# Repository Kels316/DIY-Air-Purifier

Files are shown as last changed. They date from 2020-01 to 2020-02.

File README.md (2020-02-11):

# DIY-Air-Purifier
A small DIY air purifier using off-the-shelf components for &lt;$100.

Time to assemble this project - 1hr (not including 3D print time).

Uses a 3D printed housing so you'll need a printer or access to one. You could use a printing service such as 3D Hubs.

All prices listed are in AUD.

PLEASE READ THE SECTION ON TESTING BEFORE BUILDING THIS UNIT.

## Background
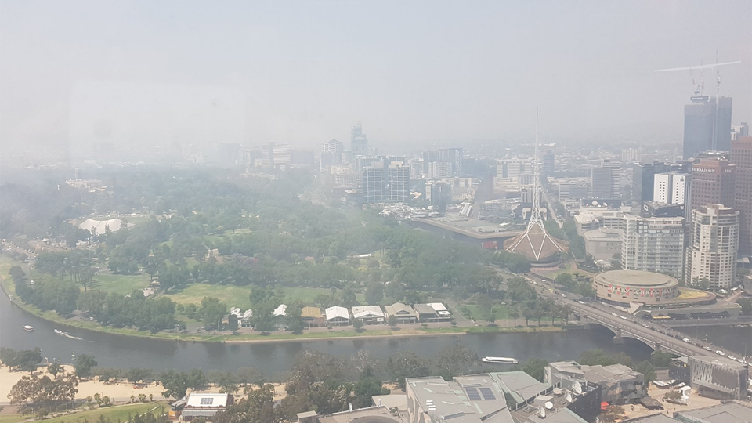
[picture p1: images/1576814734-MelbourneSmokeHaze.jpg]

In the summer of 2019/2020 Australia is experiencing unprecedented dangerous fire conditions driven by climate change. Much of the east coast of the country south of Brisbane is engulfed in deadly bushfires and air pollution ratings in cities such as Sydney, Canberra, Melbourne and many other regional cities and towns is many times the recommended safe levels of PM2.5 particles. The long term affects of the inhalation of bushfire smoke is mostly unknown at this time, but already people have died from respiratory distress bought about by the smoke-filled air.

There has been a great deal of discussion online and in the media about the use of P2 respirators and home air purifiers to reduce the effects of the bushfire smoke. However, information about the efficiacy of P2 respirators for bushfire smoke is not readily available and what information can be found suggests they may be of limited use. Health officials are continuing to recommend eliminating exposure to PM2.5 particles and bushfire smoke-related chemicals by remaining indoors if possible. Unfortunately for many people the summer heat makes indoors extremely uncomfortable and the evaporative air conditioners installed in many homes in my state of Victoria do not filter the damaging PM2.5 particles from the air. Health officials recommend using HEPA H13 air purifiers, however these are extremely expensive with even a basic unit suitable for a single room costing around $500.

With all this in mind I set about finding a way to build a low-cost, effective air purifier that would meet the minimum requirement to filter PM2.5 particles in a bedroom, so that children and at-risk people could at least sleep without inhaling these dangerous airborne contaminants.

This github sets out the process I followed to construct and test the device, as well as the BOM and 3D print STL files for recreating the device.

## Purpose
The purpose of this project is to create a small air purifier suitable for a bedroom or caravan (or similar sized space) that meets the following critiera:
  - Costs under $100 to build (in parts);
  - Can be constructed with relatively low levels of technical skill (there is soldering of two wires required);
  - Uses off-the-shelf components available in most Australian cities, or by order over the internet from Australian suppliers; and
  - Uses a HEPA H13 rated filter; and
  - Is powered from a commonly available USB powerbank.

## Method
I selected a readily available HEPA H13 rated filter normally used in cheap vacuum cleaners and available from Bunnings Warehouse. The rest of the air purifier is based around that filter. I then selected a range of 120mm computer fans with relatively high static pressure ratings (>2.0 mmAq) that could operate on 12vDC. As the fans are 12vDC I used a USB 'booster cable' which steps-up the voltage of any USB-A port from 5v to 12v; these cables are available online or from a range of electronics shops such as Jaycar.
After selecting the components I then designed a fan housing using Fusion 360 that provides the interface between the 120mm and the HEPA filter. The filter comes with a removable seal/cover at one end, so I use that end as the base of the unit and fit the fan to the top.
After basic testing with a small smoke generator to ensure the selected fans could draw air through the filter to a reasonable standard I have determined the project suitable for release so others can create their own version of this device both for use in their homes and for further testing.

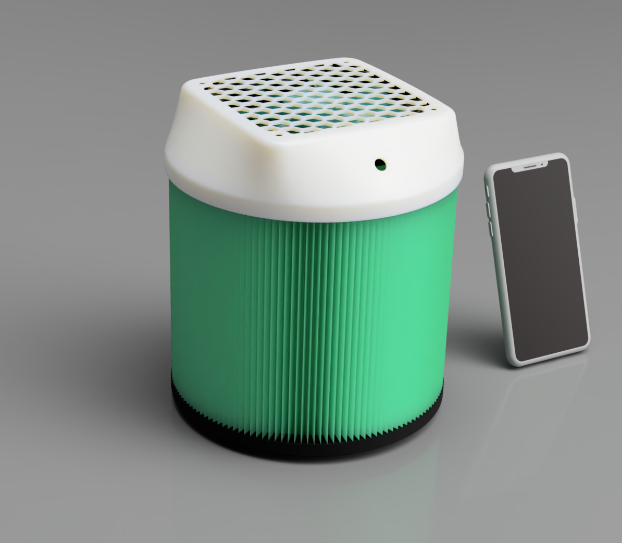
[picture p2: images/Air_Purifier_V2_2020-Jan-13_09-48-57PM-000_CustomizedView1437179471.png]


The image above shows the rendered view of the device from Fusion 360 with an iPhone X for scale. The first version of the housing used a separate fan grill but I was able to eliminate this by incorporating the hex pattern into the housing, which also saved about $7 off the cost.

## Materials
The BOM for the air purifier is:
  - 1x 120mm computer fan. I recommend you use this one: https://www.pccasegear.com/products/36033 which draws around 600ma, or if you have a larger power bank this one: https://www.pccasegear.com/products/27866 which draws around 1000ma but pushes a lot more air. The second fan is also a bit more expensive so if the budget is tight the first one will work perfectly.
  - 1x 2.5mm DC bulkhead socket: https://www.jaycar.com.au/2-5mm-bulkhead-male-dc-power-connector/p/PS0524. This allows you to plug the device in with the USB booster cable to supply 12vDC to the fan.
  - 1x 12v USB booster cable: https://www.jaycar.com.au/universal-usb-12v-step-up-power-cable/p/PP1978 Ensure you get the 12v version as these do come in 9v also and that wont work.
  - 1x HEPA H13 filter: https://www.bunnings.com.au/powerfit-h13-hepa-cartridge-filter_p6210793. Ensure you get this exact filter as the housing is dimensioned to fit over the end. Other filters with the same diameter may work, but are untested. This filter comes with an end-piece that will be the base of your device, so ensure this is in the box.
  - 1x USB power bank. Any power bank that can supply 5v >1amp will work but for best results choose one at least 10,000maH that supports pass-through charging. This allows you to use the battery as a UPS for the air purifier and run it continuously from a mains power, with  the battery being used for power outages.
  - 1x 3D printed fan housing. The STL file can be found in: [fan_housing](https://github.com/Kels316/DIY-Air-Purifier/blob/master/3D_print_files/fan_housing.stl)
  - 4pin fan cable: https://www.pccasegear.com/products/35666/cablemod-4-pin-fan-to-3x-4-pin-fan-y-cable-black-30cm. This cable is cheap and gives you three female plugs so you can make multiple devices with the one cable.
  - Heatshrink tubing 8mm (30mm long).
  - 4x rubber fan screws: https://www.pccasegear.com/products/34741/noctua-black-chromax-anti-vibration-mounting-bolts-20-pack. These unfortunately only come in a pack of 20, so you may find them in smaller amounts at other outlets. Alternatively you can use 4mm screw heat bolts and nuts, you will need to check the length you need depending on the thickness of your fan. For the fans I linked above you would need 30mm bolts.

### 3D printing notes
Just a couple of notes about the 3D print files.
  - I designed the fan housing using Fusion 360 and exported STLs from there.
  - I tweaked the design a number of times to get it to print easily on my Ultimaker 2+. You'll see in the images here (the magenta housing) an early version where the edges curled up badly. I recommend you print with a brim and a heated buildplate as that's what I have used.
  - If you have a printer with a smaller buildplate I have included a folder in [3D_print_files](https://github.com/Kels316/DIY-Air-Purifier/tree/master/3D_print_files) with a version of the housing I split into 4 so it can be printed in parts then glued together. I have not tested this print at all so if you do print it please let me know how it goes. If there are changes required that's easily done.
  - I've been printing in PLA with no requirement for supports on the default Cura settings for Ultimaker PLA, except I turn down the buildplate temp to 50ºc after the first layer, which helps prevent the edges curling. If you print in other materials then let me know how it goes.

## Tools
You will need the following tools to assemble the device:
  - Soldering iron and solder
  - Pliers (with wire cutters)
  - Scissors
  - Multimeter (to determine correct polarity for the wiring of the socket)
  
## Assembly
### Step 1
Assemble the wiring harness for the 2.5mm socket.
- Take the 4pin fan cable and cut one of the female plugs off leaving about 10cm of cable on the plug.
- Trim back the cable protective sleeve with the scissors leaving about 2cm of exposed wires.
- If you use the cable I linked above to make this harness you need the orange (+) and black (-) wires, other cables may differ so check before you go further you have the correct wires.
- Keeping the orange and black wires the length you cut previously, cut the other two wires off shorter so they will be inside the cable sheath and out of the way.
- Strip and tin the orange and black wires with new 60/40 solder and place on the heatshrink tubing over the top of the cable protective sheath.
- Determine the correct terminal lugs on the 2.5mm socket using the multimeter. Then solder the + and - wires to the correct terminals.
- Pull the heatshrink over the socket lugs and shrink it with a heat gun or flame.
- The completed wiring harness should look similar to this
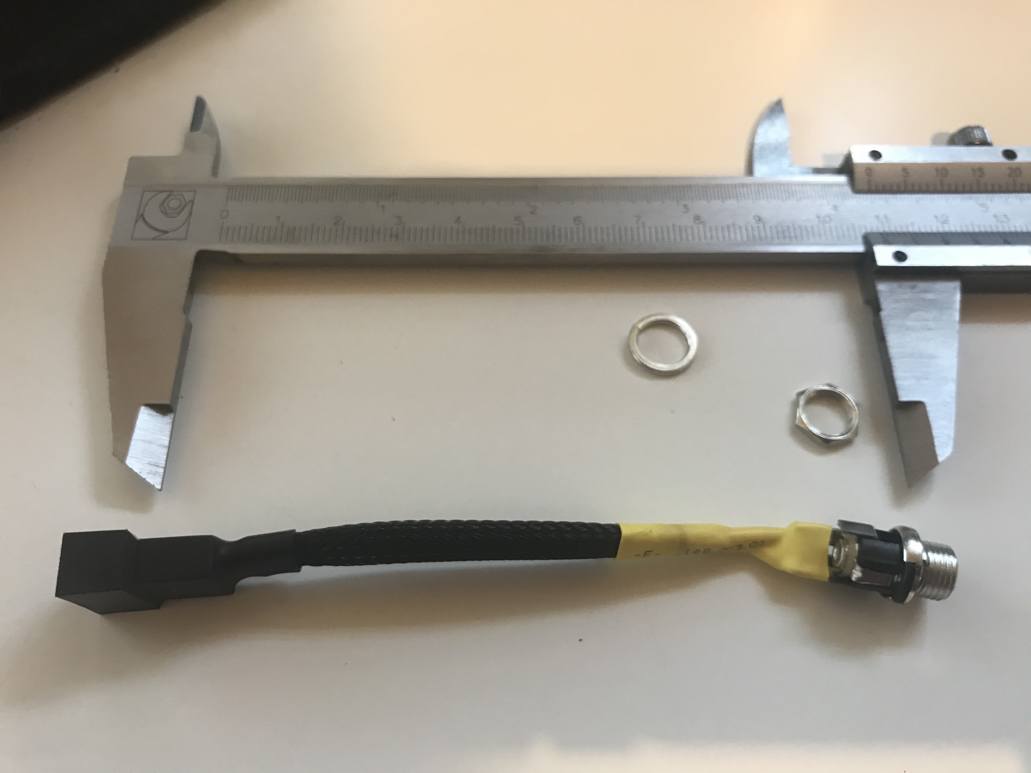
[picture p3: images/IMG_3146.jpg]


### Step 2
Assemble the fan housing.
- Take the 3D printed housing and insert the 2.5mm socket from the inside, and fix in place using the supplied washer and nut. Tighten down with your pliers so it is snug but don't go crazy, you don't want to crack the housing.
- Place the fan inside the housing with the writing facing towards the square end, this will ensure the fan draws air through the filter rather than pushing air into the filter. It wont make a huge difference to the performance of the device, but it's good practice to have clean air running over the fan. Use the 4 rubber fan mounts (or bolts if you use that method) to fix the fan into the case, then plug the fan cable into the wiring harness from step 1.
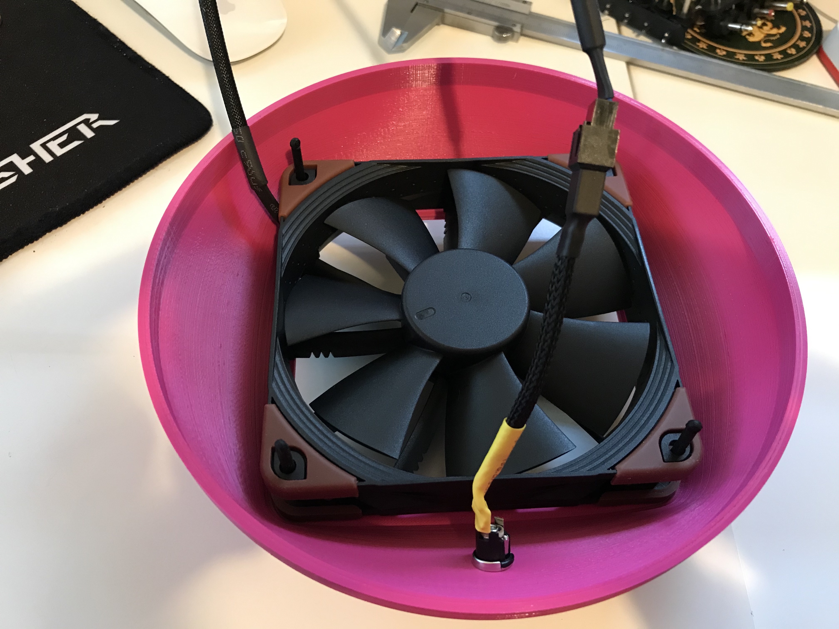
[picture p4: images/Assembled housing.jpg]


### Step 3
Assemble the device.
- Take the fan housing assembly and place it over the open end of the HEPA filter, taking care to work around the edge of the rubber ring on the filter itself so a good seal is make on the inside of the housing.
- Ensure the base cover is installed firmly in the filter housing.
(note the images below are of an early version with no integrated fan grill, the assembly is identical otherwise. I'll update these with better images later)

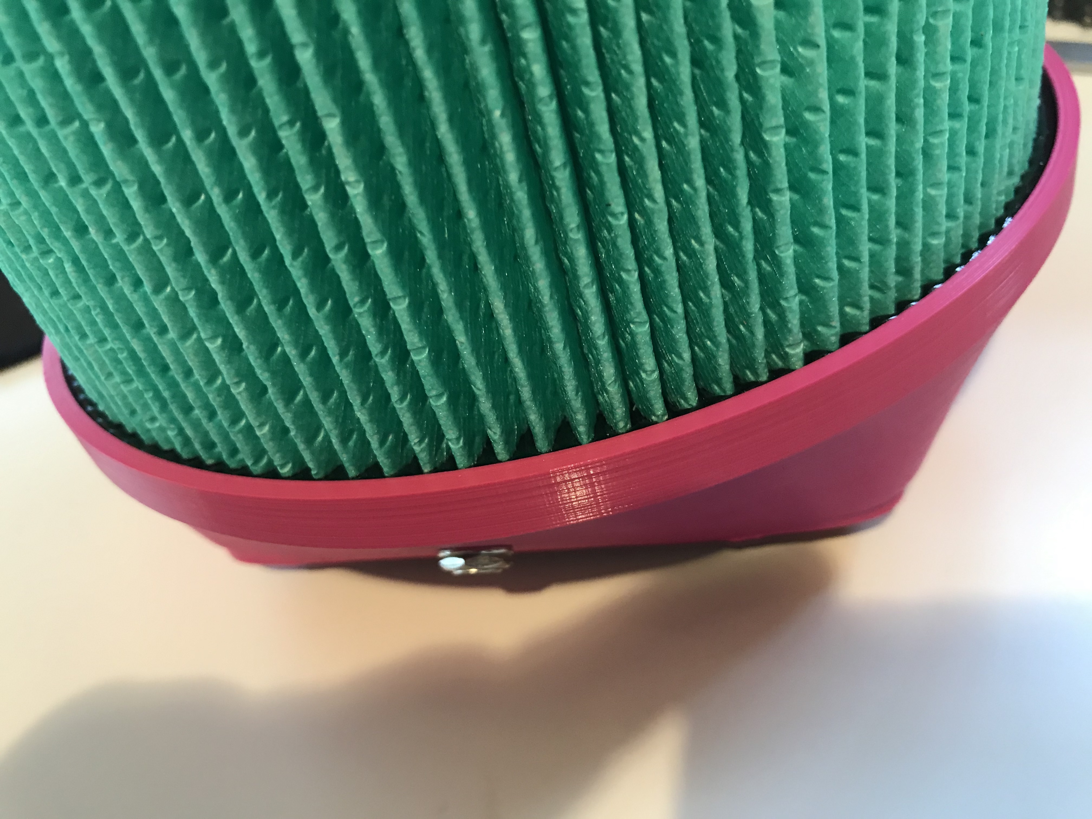
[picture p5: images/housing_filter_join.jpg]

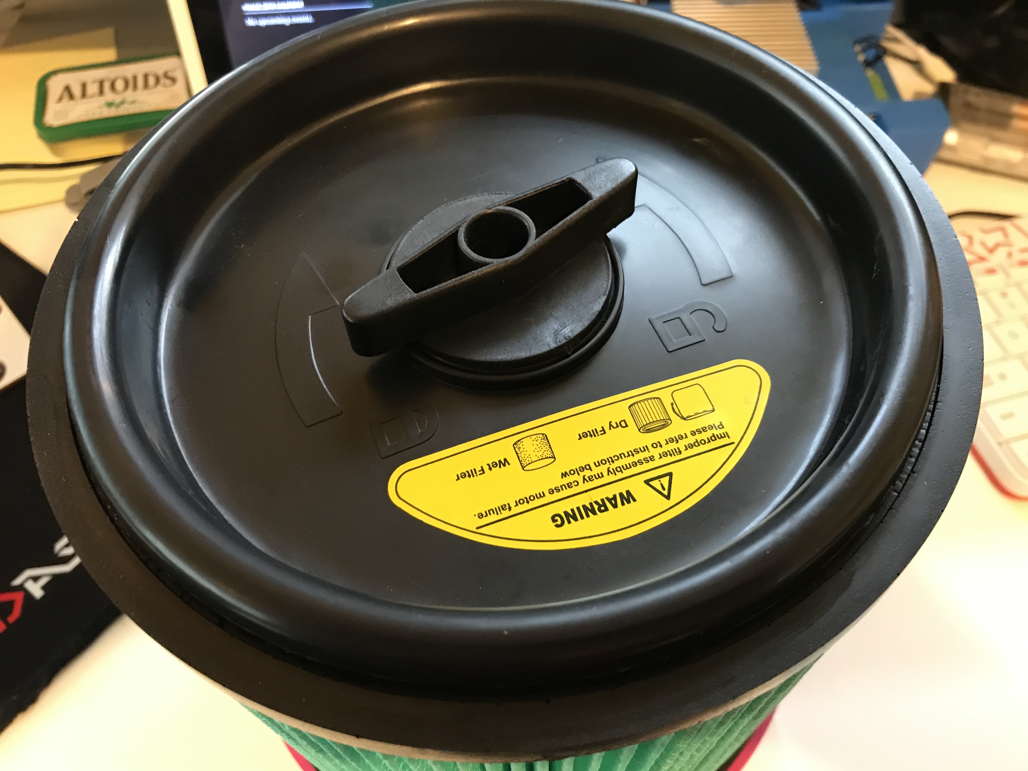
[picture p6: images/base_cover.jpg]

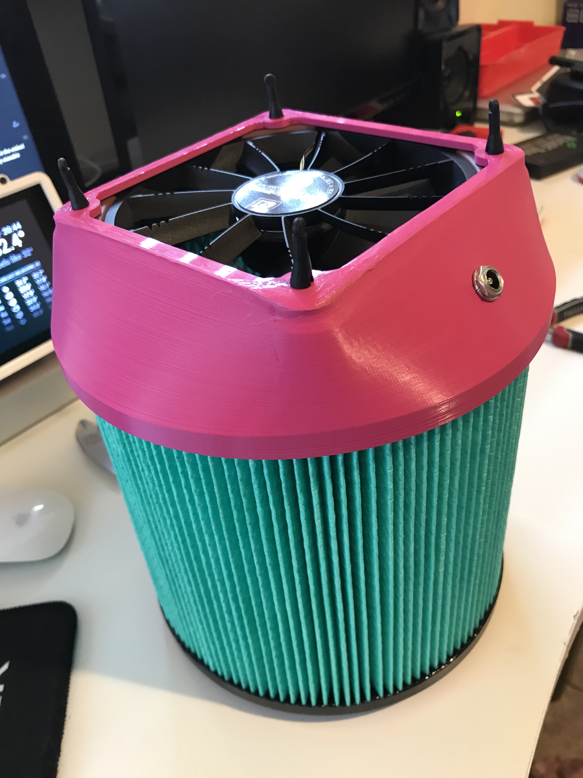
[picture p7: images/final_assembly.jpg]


### Step 4
Power up and test.
- Assemble the USB cable with the 2.5mm plug. In the kit linked above it is the largest suppled plug, with the white tip.
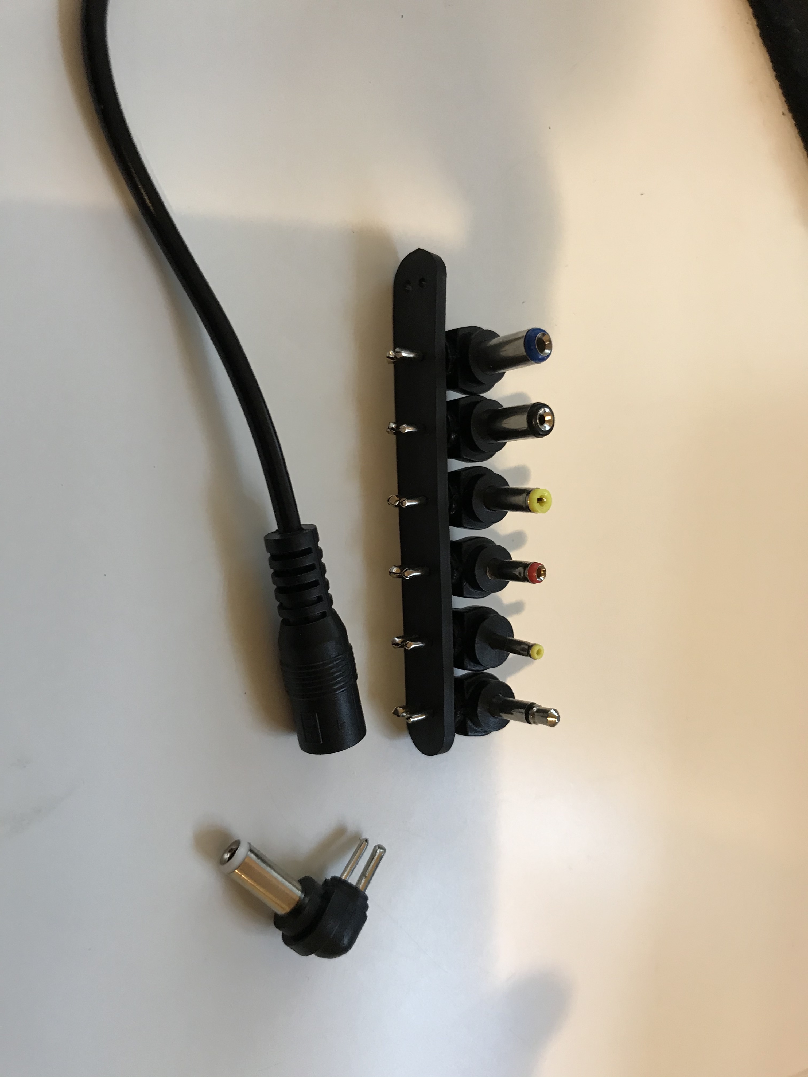
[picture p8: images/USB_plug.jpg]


- Plug the cable into the device and your USB power bank and the fan should start running. If the fan doesn't work you should begin troubleshooting. Start with checking your powerbank is charged and turned on to supply power. I have a couple of battery packs that don't work to supply power to the air purifier, even though they are rated well above the requirement, I'm not sure why but it seems like some devices can't supply the surge current required to start the fan.
- Note that not all power banks can support pass-through charging and depending on the fan you select you may find the pack cannot charge faster than you run it down. The more expensive fan I linked above will draw around 1amp or a little above, and if you use this fan you need to make sure your charger can supply above 1amp (comfortably) to keep your battery charged. The power bank in the image below is one I use for testing in my office, it's not suitable to run the device for long periods.
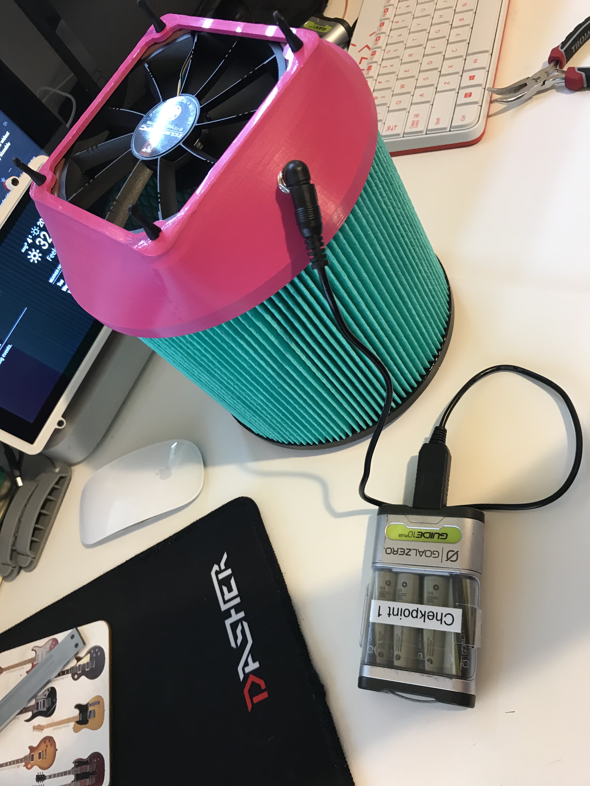
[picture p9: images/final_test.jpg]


## Initial test results
Since initially publishing this project additional people have come forward to help with refining and testing the air purifier. Recently we had some robust tests conducted on the Clean Air Delivery Rate (CADR) prduced by this unit. Unfortunately the current configuration of the air purifier produces a very low CADR of ~16m3/hr, this equates to 6 ACH (air exchanges per hour) in a 1.6m2 space - not enough to be effective as a small bedroom air purifier.

We are continuing to work on ways to improve the performance of the air purifier without compromising the DIY nature, or significantly increasing the cost. There are some challenges to be overcome but I'm confident we'll be able to update the project soon with a design that is much more effective. Watch this space!

## Final remarks
This is a DIY project requiring basic skills including soldering. Selecting an appropriate power supply will require some basic knowledge of electricity. I've tried to keep everything as simple as possible and this isn't a consumer-grade product. The initial testing of this design has shown it is not an effective replacement for a commercial air purifier at this stage, but work continues to improve it. You should build and use this device at your own risk, no liability is implied or accepted.

## Request for assistance
If you can assist with improving this project by more rigorous testing then please get in touch with me at info@phasezero.com.au or via this repo.

### Licence
This work is licenced under a Attribution-NonCommercial-ShareAlike 3.0 Australia licence. 
[https://creativecommons.org/licenses/by-nc-sa/3.0/au/](https://creativecommons.org/licenses/by-nc-sa/3.0/au/)

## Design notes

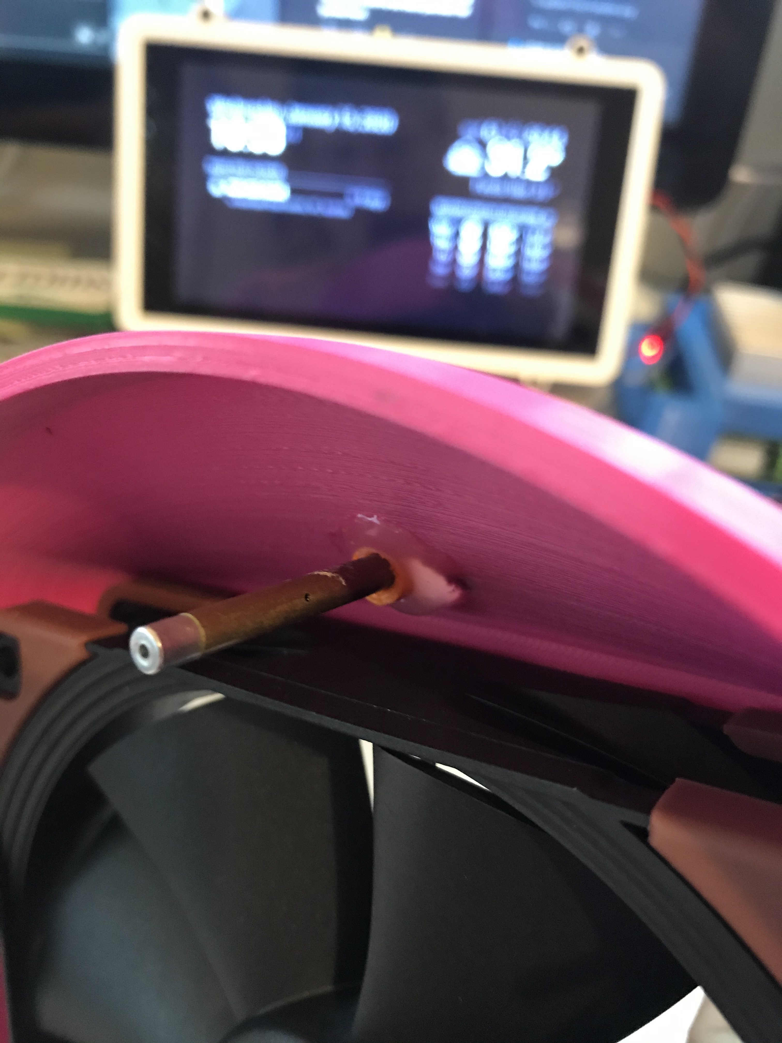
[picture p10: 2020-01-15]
images/airspeed3.jpg

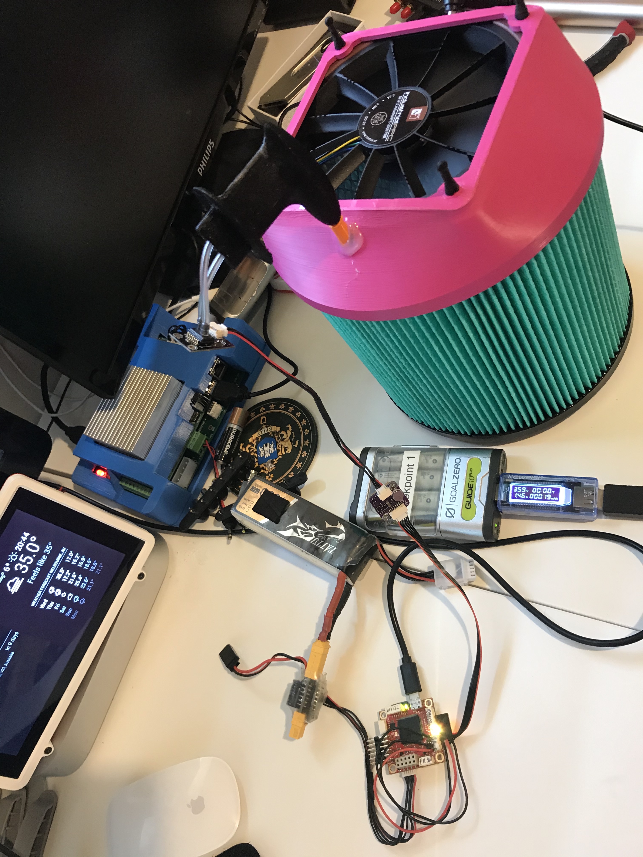
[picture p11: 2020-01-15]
images/airspeed data.jpg

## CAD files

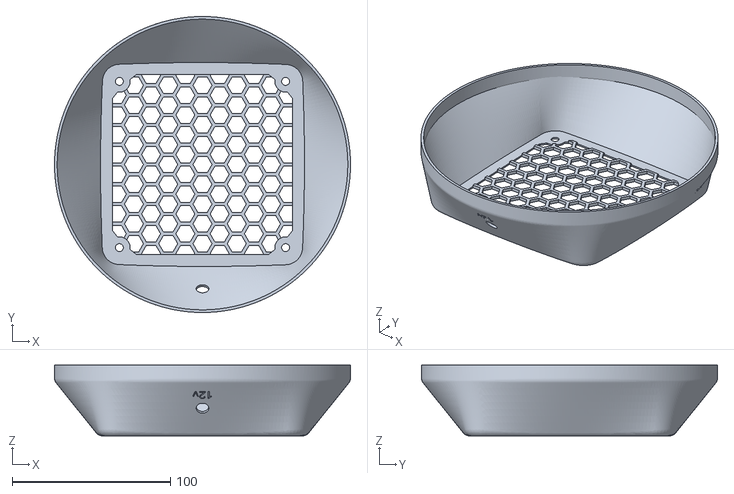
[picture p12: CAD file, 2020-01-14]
3D_print_files/fan_housing.stl
187.0 x 187.0 x 44.7

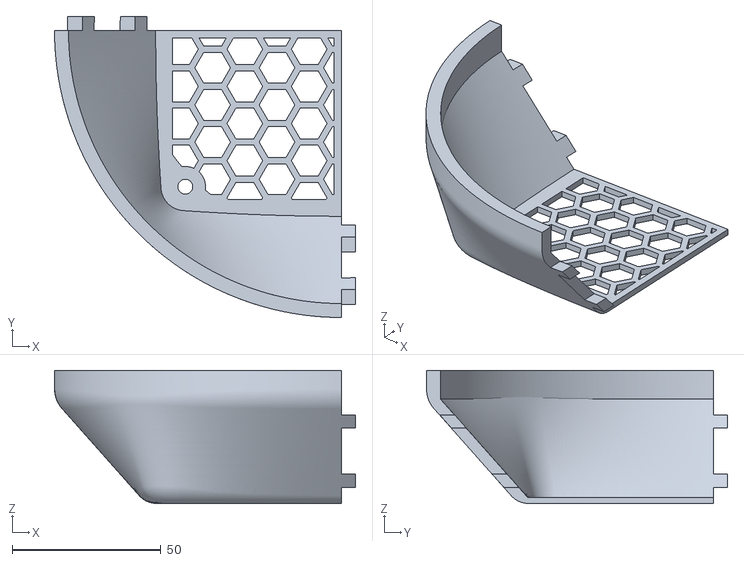
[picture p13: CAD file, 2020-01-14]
3D_print_files/small_printer_files/fan_housing_small_printer_1.stl
101.2 x 101.2 x 44.7

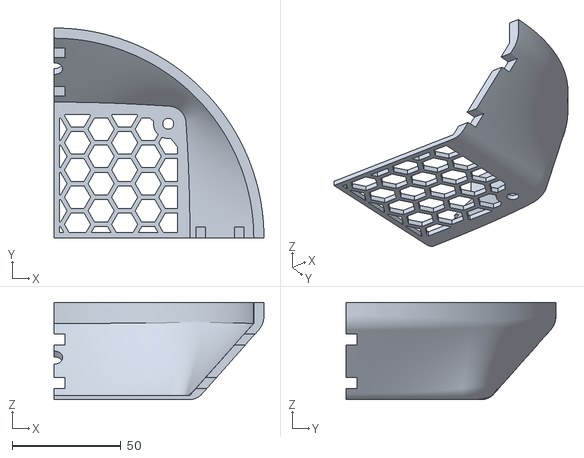
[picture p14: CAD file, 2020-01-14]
3D_print_files/small_printer_files/fan_housing_small_printer_4.stl
96.5 x 96.5 x 44.7

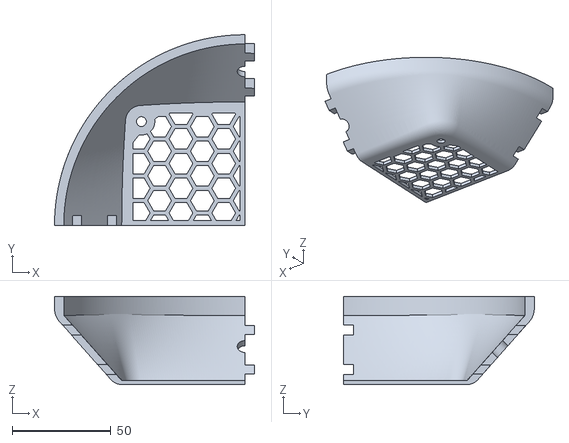
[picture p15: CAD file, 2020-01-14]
3D_print_files/small_printer_files/fan_housing_small_printer_3.stl
101.2 x 96.5 x 44.7

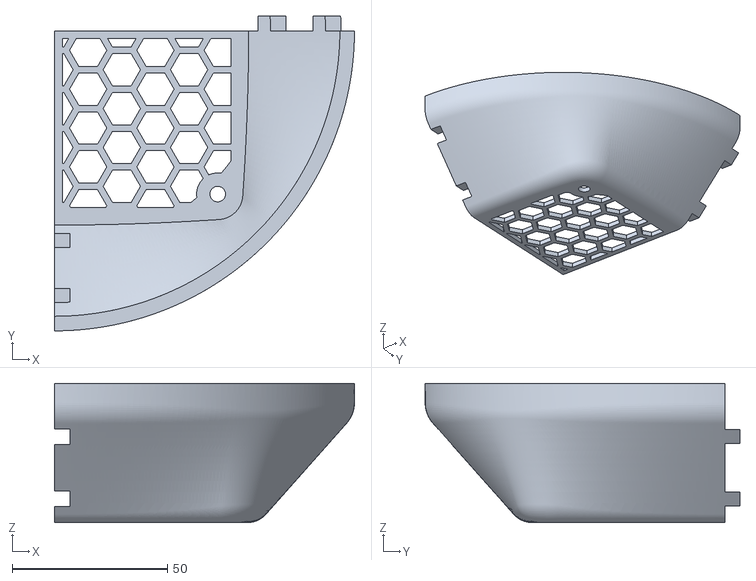
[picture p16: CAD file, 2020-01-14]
3D_print_files/small_printer_files/fan_housing_small_printer_2.stl
96.5 x 101.2 x 44.7

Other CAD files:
3D_print_files/AP_Top v5.f3d

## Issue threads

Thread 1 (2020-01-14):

Small typo on link to USB cable

grandaspanna, 2020-01-14:
There's just an extraneous character at the end of the link to the Jaycar 12V usb booster cable in the README. Got the 3D printer humming away...

Kels316, 2020-01-14:
thanks, fixed it :)

grandaspanna, 2020-01-14:
Awesome. Did some rummaging/ruminating – would something like this be useful for simplifying things? Should be plug in and go.

USB->12V (up to 1.5A ish) converter on a single board with micro USB connector and header for FAN. TBH – I don’t know the exact connector used for chassis fans and what the pinouts are, but that’s easy enough to change.

Parts cost should be under $20 and I can assemble limited quantities at zero cost, where quantities is a number between 1 and 50. Any more than that and I’d probably throw it to an offshore manufacturer.

If it’s not obvious, the board is intended (designed is too strong a word) to sit inside the case and then the USB socket is accessible from the outside.

I haven’t really thought about dimensions/shape, but also easily enough sorted.

Oh, Nokia 3310 for reference 😉

Phil.

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

Kels316, 2020-01-14:
I think I’m missing an attachment?

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

grandaspanna, 2020-01-14:
Weird. Gimme a few minutes, just grabbing a coffee.

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

grandaspanna, 2020-01-15:
Trying again…

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

grandaspanna, 2020-01-15:
Ah, looks like attachments don't work via email.
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

Kels316, 2020-01-15:
Ah ok that looks interesting. For this version I’m trying to keep the components to things people can buy over-the-counter or online from local (Aus) suppliers. Definitely interested in another version that’s a bit more advanced for people who want additional features. This could be incorporated into that.

The fans use a 4 pin connector but I’m not sure what the actual name of it is, should be easy enough to find it on digikey or similar

Cheers,

Adam

 <http://www.phasezero.com.au/>
Adam Kelly <mailto:adam.kelly@phasezero.com.au>
Director | Phase Zero Consulting Services <http://www.phasezero.com.au/>
0400 589 095 | www.phasezero.com.au <tel:+61 400 589 095>

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

grandaspanna, 2020-01-15:
Cool. I'll make a couple up for my own purposes. Apart from the PCBs, I source the components from local suppliers when I do my own assembly. Purely for hobby purposes, I sell a few electronic bits on Tindie. Their fees and PayPal fees are a pain, but not aware of too many alternatives.

Got an old board with the same basic layout handy, so I'll test that. Found a local shop that has a twin pack of the Corsair fan and ordered those. The 3D printer yielded fruit overnight, so now on to getting the filter and putting it all together.

Kels316, 2020-01-15:
love it! Keen to see how the build goes with that board.

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

Kels316, 2020-01-15:
I have a slack channel set up for this project too, if you want to join in the discussions.

https://join.slack.com/t/phase-zero-workspace/shared_invite/enQtOTA2MzcxMTAzMzAwLWM1MTZkY2FiNTQ0MWFhZTM2ZDMwN2FjMDcyY2MyZDQxMGQ1MmNiMTNlMGIxYzEzMDE3ODY5NTg5MmExMGEyO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

Cheers,

Adam

 <http://www.phasezero.com.au/>
Adam Kelly <mailto:adam.kelly@phasezero.com.au>
Director | Phase Zero Consulting Services <http://www.phasezero.com.au/>
0400 589 095 | www.phasezero.com.au <tel:+61 400 589 095>

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

grandaspanna, 2020-01-15:
Pics of this evening's testing. Given me enough confidence to order some bits.
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

Kels316, 2020-01-15:
nice one. If you have a model of the board you can flick me I’ll make a version of the fan housing that has a place to mount it, unless you’re already doing that?

grandaspanna, 2020-01-15:
See if this works. It's not necessarily final, but based on last night's testing, should work ok.
[air_filter_pcbv2.zip](https://github.com/Kels316/DIY-Air-Purifier/files/4068058/air_filter_pcbv2.zip)

Kels316, 2020-01-15:
awesome, thanks

Closed 2020-01-14.

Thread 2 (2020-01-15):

Airflow measurement

Kels316, 2020-01-15:
So I rigged up an airspeed sensor from old drone parts and made an adapter to insert the pitot tube into the fan housing. After calibration I ran the fan for a while and took readings, got around ~2m/s average. I cross checked this with a handheld anemometer and got 7.5kph which is about the same so it seems like that's probably reasonably accurate.

I'm not an HVAC person so I'm not sure which part of the housing I should use to calculate the CFM - the inlet (147mm) or the outlet (110mm). If anyone can assist who knows about HVAC calculations I'd really appreciate it.

As it stands I'm getting between 161-287CFM depending on which area I use. The fan I'm testing is rated to 186CFM on the box, so I'm assuming the lower of the two measurements it likely the correct one.

This puts it in the area of 10 air exchanges per hour for my home office, which is 25sqm, about the size of a small bedroom. That would indicate it's working pretty well to run the air through the filter but it seems too good for such a basic device so I suspect my methodology might be suspect.

Again, if you are familiar with these processes and measurements let me know as I'd love to get this right.

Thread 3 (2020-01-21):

PM25 measurement

gaguevaras, 2020-01-21:
If you're interested in getting another KPI to track how effective the air purifier is, you could easily build this PM25 sensor:

https://www.hackster.io/canairio-guide-team/canairio-citizen-network-for-air-quality-monitoring-bbf647

It would allow you to measure the effect your purifier has on indoor air quality by measuring how many particles under 2.5 microns per cubic meter there are before and after operating it. Good luck!

Mihaylov93, 2020-01-22:
Also there is the MQ sensor series like https://www.olimex.com/Products/Components/Sensors/Gas/SNS-MQ135/resources/SNS-MQ135.pdf

Kels316, 2020-01-30:
yes I have considered building a test bench for this, but time has been short recently. Definitely on the to-do list for the coming months.

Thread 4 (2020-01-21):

Instructions needed for filter maintenance

alfredosola, 2020-01-21:
When the device has been running for a while, it is reasonable to expect that the filter will become increasingly clogged, efficiency will drop, and eventually perhaps particles would become afloat when the fan stops.

I think instructions should be added regarding:

1. The expected lifetime of a filter
2. Whether the filter can be cleaned or not, and how to do it safely (water immersion?)
3. How to assess the status of a filter
4. Handling of a filter that ended its life

I regret that I can provide questions but not answers. Hoping someone can chime in.

Nospamas, 2020-01-21:
From experience running an off the shelf air filter for the last couple of years, this one specifically:

https://www.homedepot.com/p/Winix-FresHome-Model-P300-True-HEPA-Air-Cleaner-with-PlasmaWave-Technology-113100/205445246

Slightly out of order as it makes more sense to answer the questions this way:

1. HEPA filter is changed out once per year. This obviously will vary depending on flow rate, environmental conditions and whether you can add a pre filter. What you're looking for is good air flow such that the air filter continues to exchange a large portion of the air in any space, once the flow rate is reduced over time this will no longer happen. I'm not sure that this duration can be assessed without testing the filter in operation.
3. Over time the filter will become noticeably browner with small particulates. As the filter becomes more clogged with dust you'll see a reduction in flow rate.
2. Washable HEPA filters do exist, though I can't find any information from the specific one chosen in this guide suggesting that this is so.
4. Carefully bagging the used filter so as to not knock too many particulates back into the air and simply throwing it out seems to be the standard method for non reusable filters. Again, no suggestion that the chosen filter is reusable or recyclable, though I'd be happy to be corrected.

Finally: As noted in part 1 extension of the filters life might be achieved by adding a larger non-HEPA filter. In the commercial model we use this is achieved by a much larger mesh filter in front of the HEPA, does a good job of filtering out large particulates such as pet hair or dust bunnies.

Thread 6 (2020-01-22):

Foam wrap to block larger items

Turophile, 2020-01-22:
Please consider adding a layer of soft foam wrapped around the outside to trap hair and other large dust items. The layer should be removable so it can be cleaned or replaced when necessary. This should also enable the main filter to last longer. May even make the purifier more aesthetically pleasing.

Kels316, 2020-01-30:
A few people have suggested this. I'm definitely open to the idea and I think it could be done cheaply, but we really need to get some decent testing of the airflow before adding any more filter layers. Thanks for the comment :)

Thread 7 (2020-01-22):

Consider using NF-A12x25 PWM fan because it come with USB adapter cable?

tuananh, 2020-01-22:
Very nice work! Have you considered using one of our 5V fans such as the NF-A12x25 PWM? https://noctua.at/en/nf-a12x25-5v-pwm

These come with USB adaptor cables, so this would make it even easier to power the fan from a regular power bank.

https://twitter.com/Noctua_at/status/1219875318908977152

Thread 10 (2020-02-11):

Exact filter dimensions

danielkucera, 2020-02-11:
Could you please provide exact dimension of that hepa filter?

So we can test possible replacements availabe in shops in EU.

I'm thinking about this one:
https://www.sackyvysavace.cz/cz-detail-1274051-filtr-hepa-jolly-hf16-pro-karcher-6.414-552.0-6.414-525.html

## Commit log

2020-01-14 Create test
    these files are for printers with build plates that can't accommodate the full size housing. Requires to be printed in four pieces and glued together. I have not tested this print at all.
2020-01-14 Update README.md
    fixed typo in fan cable link
2020-02-11 Replace test info with new data
    New test data shows the device is less effective than we initially thought. Work continues to improve it.
2020-05-14 Add files via upload
    Updated version of print file with 3mm fillet on inside edge.
    [AP_Top v5.f3d]
